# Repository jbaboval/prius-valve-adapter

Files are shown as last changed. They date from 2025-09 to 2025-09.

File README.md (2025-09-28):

# VintageAir to Prius Heater Valve Adapter

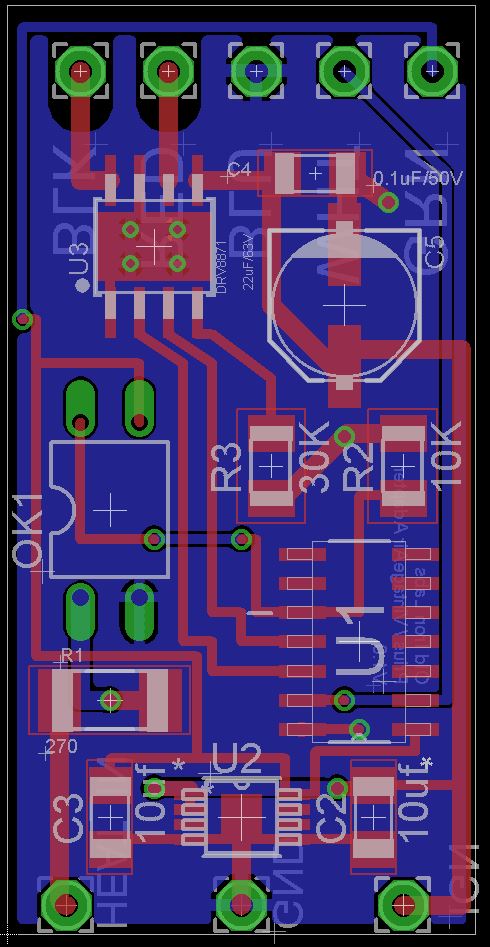
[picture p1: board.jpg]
Board Overview


Vintage Air systems ship with a simple on/off heater control valve which stops coolant flow to the heater core when the AC is on. 

Chevy GenV small block engines (L86/LT1, L83, etc) require constant flow through the heater loop, so a simple on/off valve is not suitable.

2nd Generation Toyota Prius' (2004-2009) have an ideal three-way coolant valve that is relatively inexpensive. (Sub-$20), but uses an ECU controlled motor. (Part number 16670-21010)

This adapter connects the Vintage Air one-wire on/off signal to the five-wire Prius valve.

The adapter is based on an ATTiny24, with a DRV8871 motor driver. It is powered by an AP7583AQ voltage regulator, and the input level is shifted from IGN voltage by a PC817C optical coupler.

# Pinout

The Prius valve has a brushed DC motor that turns a ball valve through a worm drive. The valve stem is connected to a simple potentiometer. The motor and potentiometer pins are exposed in the five wire connector:

* Red - Brushed DC Motor
* Black - Brushed DC Motor
* White - Potentiometer Wiper
* Green - Potentiometer +
* Blue - Potentiometer -

The Vintage Air controller has one blue wire that is either N/C or +12v when the AC is on.

One side of the board has labeled pins for the color coded Prius valve wires. The other side takes +12v, GND, and the VintageAir in.

# BOM

| Part Number | Quantity | Link |
|---|---|---|
| ATTiny24A-SSU | 1 | https://www.digikey.com/en/products/detail/microchip-technology/ATTINY24A-SSU/2050982 |
| DRV8871 | 1 | https://www.digikey.com/en/products/detail/texas-instruments/DRV8871DDAR/5639726 |
| AP7583AQ-50MP-13 | 1 | https://www.digikey.com/en/products/detail/diodes-incorporated/AP7583AQ-50MP-13/17736704 |
| PC817C | 1 | https://www.amazon.com/dp/B0DJ8ZBHJ2 |
| 1206 10uF Ceramic Capacitor | 5 | |
| 1206 0.1uF Ceramic Capacitor | 1 | |
| 22uF/63v Capacitor | 1 | https://www.digikey.com/en/products/detail/kemet/EDK226M063S9HAA/6597717|
| 2010 270ohm 1.25W Resistor | 1| https://www.digikey.com/en/products/detail/te-connectivity-passive-product/CRGP2010F270R/8577255 |
| 1206 10K Resistor | 1| |
| 1206 30K Resistor | 1| |

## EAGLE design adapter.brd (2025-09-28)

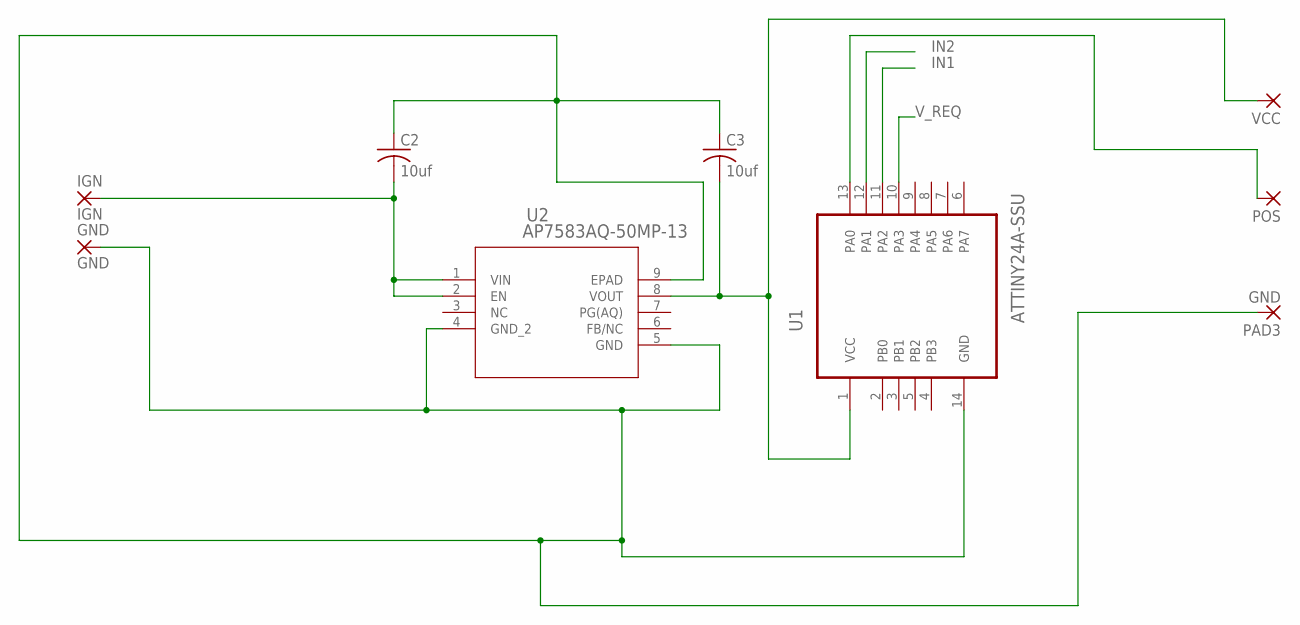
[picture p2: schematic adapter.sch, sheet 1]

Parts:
C2, C3: 10uf; C1206
GND: GND; 2,15/1,0
IGN: IGN; 2,15/1,0
PAD3: GND; 2,15/1,0
POS: 2,15/1,0
U1: ATTINY24A-SSU; SOIC127P600X175-14N
U2: AP7583AQ-50MP-13; MSOP-8EP_DIO
VCC: 2,15/1,0

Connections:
GND: C2.1, C3.1, GND.1, PAD3.1, U1.14 (GND), U2.4 (GND_2), U2.5 (GND), U2.9 (EPAD); also elsewhere on the board
IGN: C2.2, IGN.1, U2.1 (VIN), U2.2 (EN); also elsewhere on the board
IN1: U1.11 (PA2); also elsewhere on the board
IN2: U1.12 (PA1); also elsewhere on the board
unnamed: POS.1, U1.13 (PA0)
VCC: C3.2, U1.1 (VCC), U2.8 (VOUT), VCC.1; also elsewhere on the board
V_REQ: U1.10 (PA3); also elsewhere on the board

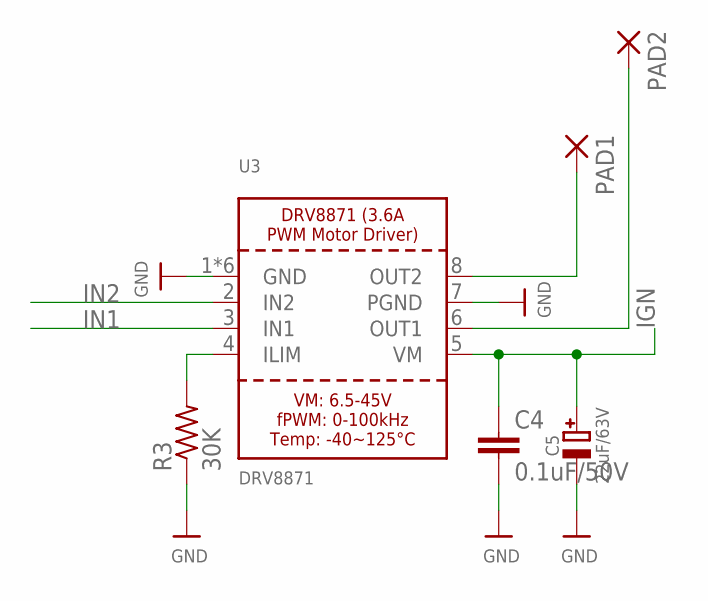
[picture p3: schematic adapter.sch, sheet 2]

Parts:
C4: 0.1uF/50V; C1206
C5: 22uF/63V; PANASONIC_D
PAD1, PAD2: 2,15/1,0
R3: 30K; M1206
U3: DRV8871; HSOP8

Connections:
GND: C4.2, C5.-, R3.1, U3.1 (GND), U3.7 (PGND), U3.GND, U3.P$1 (GND), U3.P$2 (GND), U3.P$3 (GND), U3.P$4 (GND); also elsewhere on the board
IGN: C4.1, C5.+, U3.5 (VM); also elsewhere on the board
IN1: U3.3 (IN1); also elsewhere on the board
IN2: U3.2 (IN2); also elsewhere on the board
unnamed: R3.2, U3.4 (ILIM)
OUT1: PAD2.1, U3.6 (OUT1)
OUT2: PAD1.1, U3.8 (OUT2)

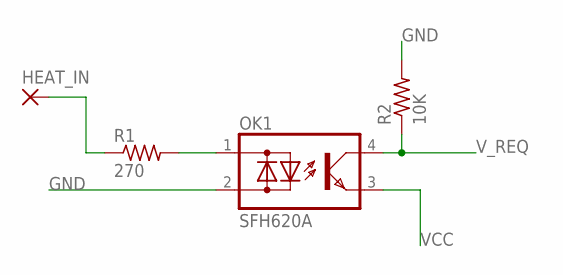
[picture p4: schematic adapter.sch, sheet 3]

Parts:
HEAT_IN: 2,15/1,0
OK1: SFH620A; DIL04
R1: 270; R2010
R2: 10K; M1206

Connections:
GND: OK1.2 (AC2), R2.2; also elsewhere on the board
unnamed: OK1.1 (AC1), R1.2
unnamed: HEAT_IN.1, R1.1
VCC: OK1.3 (E); also elsewhere on the board
V_REQ: OK1.4 (C), R2.1; also elsewhere on the board

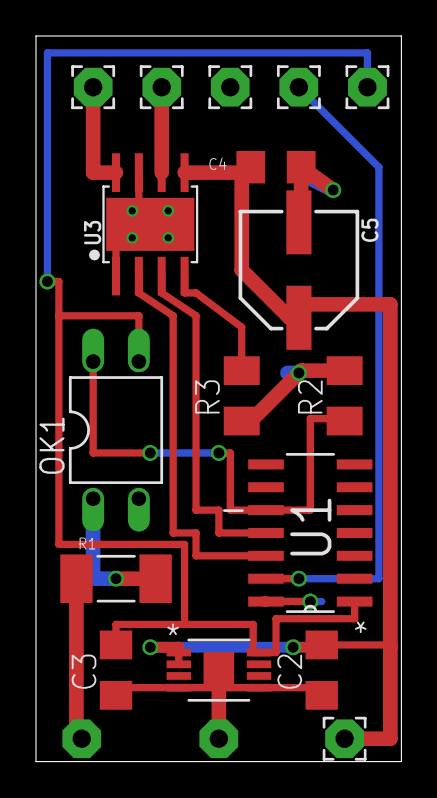
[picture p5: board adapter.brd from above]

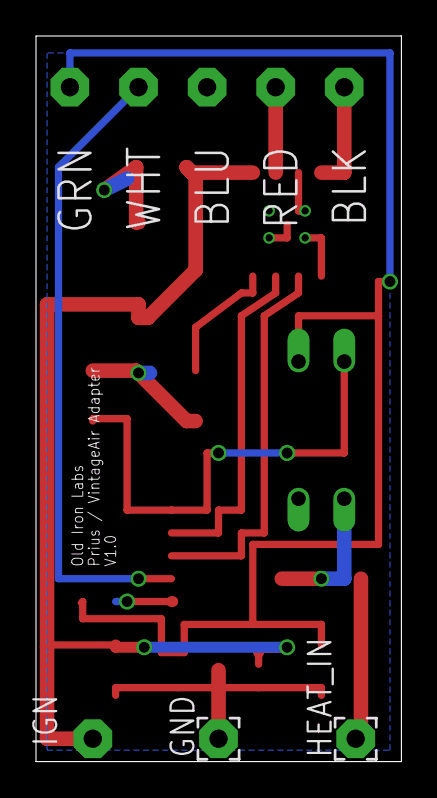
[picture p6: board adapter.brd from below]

Board: 2 copper layers, 20.3 x 40.3 mm, 19 parts (2 on the bottom side), 12 nets.

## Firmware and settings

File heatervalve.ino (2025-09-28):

#define MOTOR_IN1 A2
#define MOTOR_IN2 A1
#define POS_IN    A0
#define REQ_IN    A3

#define POS_CURRENT 0
#define POS_OPEN 1
#define POS_CLOSED 2

typedef struct {
  int position;
  int plusTolerance;
  int minusTolerance;
} goal_t;

goal_t goal_positions[] = {
  { 512, 1024, 1024}, // Always matches current position
  { 80, 30, 80 },      // Valve is open to heater core
  { 950, 75, 0 },     // Valve is closed, bypass heater core
};

int goal;

void setup() {
  // put your setup code here, to run once:

  pinMode(POS_IN, INPUT);
  pinMode(REQ_IN, INPUT);
  pinMode(MOTOR_IN1, OUTPUT);
  pinMode(MOTOR_IN2, OUTPUT);
 
//  Serial.begin(9600);

  goal = POS_CURRENT;
}

void openValve() {
  goal = POS_OPEN;
}

void closeValve() {
  goal = POS_CLOSED;
}

void stopValve() {
  goal = POS_CURRENT;
}

void setSpeed(int pwm) {
  // Negative direction is on MOTOR_IN2, Positive direction is on MOTOR_IN1
  if (pwm == 0) {
      digitalWrite(MOTOR_IN1, LOW);
      digitalWrite(MOTOR_IN2, LOW);
  } else if (pwm < 0) {
      digitalWrite(MOTOR_IN1, LOW);
      analogWrite(MOTOR_IN2, abs(pwm));
  } else {
      digitalWrite(MOTOR_IN2, LOW);
      analogWrite(MOTOR_IN1, pwm);
  }
}


int distanceFromGoal(int position, goal_t goalPos) {

  if (position == goalPos.position) {
    return 0;
  }
  
  if (position > (goalPos.position - goalPos.minusTolerance)) {
    if (position <= (goalPos.position + goalPos.plusTolerance)) {
      return 0;
    }

    return goalPos.position - position;
  }

  if (position >= (goalPos.position - goalPos.minusTolerance)) {
    return 0;
  }

  return goalPos.position - position;
}

void loop() {
  static int position = 0;
  static int currentPWM = 0;
  static int targetPWM = 0;
  static int accel = 25;
  static int tick = 0;
  static int request = 0;
  static int previous_req = 0;
  static unsigned long millis_powered = millis();

  unsigned long current_millis = millis();

  // put your main code here, to run repeatedly:
  position = analogRead(A0);
  request = digitalRead(A3);

  if (request != previous_req) {
    // Protect against stuck. Remember how long we've been trying 
    // to obtain the requested position. Stop after a while. 
    // Retry when the request changes.
    millis_powered = current_millis;
  }

  goal = request ? POS_OPEN : POS_CLOSED;

  goal_t goalPos = goal_positions[goal];

  int distance = distanceFromGoal(position, goalPos);

  if (distance > 0) {
    targetPWM = 255;
  } else if (distance < 0) {
    targetPWM = -255;
  } else {
    targetPWM = 0;
  }

  if (targetPWM < currentPWM) {
    if ((currentPWM - targetPWM) < accel) {
      currentPWM = targetPWM;
    } else {
      currentPWM -= accel;
    }
  } else if (targetPWM > currentPWM) {
    if ((targetPWM - currentPWM) < accel) {
      currentPWM = targetPWM;
    }
    currentPWM += accel;
  }

  if (currentPWM == 0 || (millis_powered > current_millis)) {
    millis_powered = current_millis;
  }

  if ((current_millis - millis_powered) < 30000) { // Don't let the motor be on for more than 30s
    setSpeed(currentPWM);
  } else {
    setSpeed(0);
  }

//  setSpeed(currentPWM);

  delay(10);
}

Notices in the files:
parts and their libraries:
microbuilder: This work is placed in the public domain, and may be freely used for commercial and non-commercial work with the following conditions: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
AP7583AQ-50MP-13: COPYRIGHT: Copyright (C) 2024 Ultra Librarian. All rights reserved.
